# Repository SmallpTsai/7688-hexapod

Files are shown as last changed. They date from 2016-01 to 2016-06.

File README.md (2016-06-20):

# An 18 DOF Hexapod project using LinkIt Smart 7688 + PCA9685

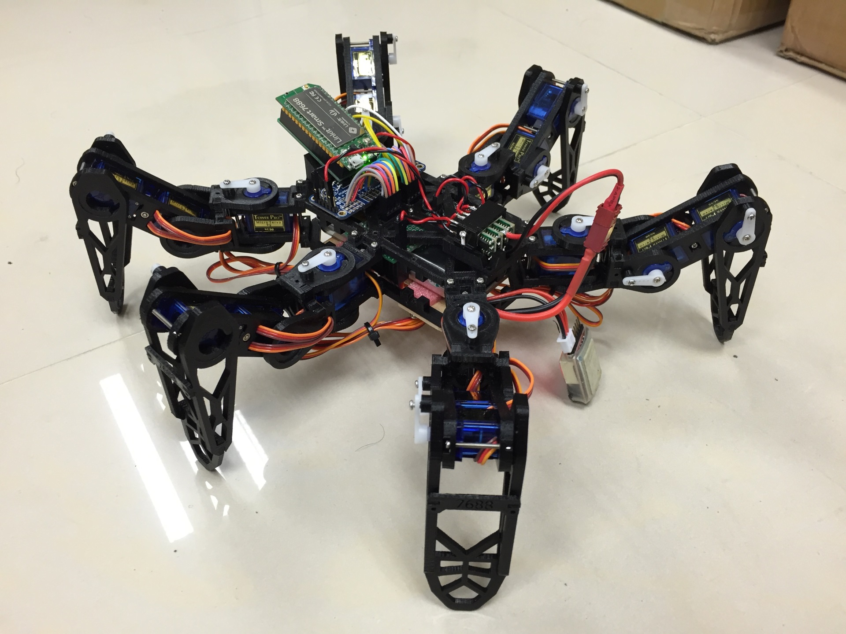
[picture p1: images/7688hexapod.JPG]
7688hexapod


Youtube video1 (http://www.youtube.com/watch?v=CbFrT2eCAvw)
[Youtube video1](https://www.youtube.com/watch?v=CbFrT2eCAvw)

Youtube video2 (http://www.youtube.com/watch?v=70pN0Rd0ca4)
[Youtube video2](https://www.youtube.com/watch?v=70pN0Rd0ca4)

## Hardware

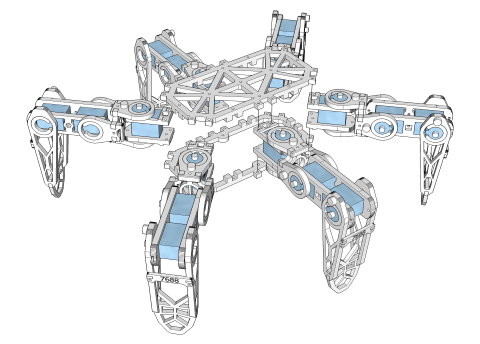
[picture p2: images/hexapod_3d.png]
* Body: 3D printed, go to [STL](STL) folder 
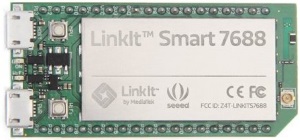
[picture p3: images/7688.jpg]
* [LinkIt Smart 7688](labs.mediatek.com/7688) 
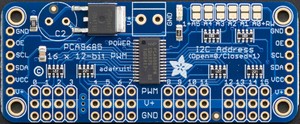
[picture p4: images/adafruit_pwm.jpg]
* [Adafruit 16-channel PWM driver (PCA9685)](https://www.adafruit.com/product/815) 
* SG-90 mini servo x 18 
* DC/DC Buck Voltage regulator (Mini 360 from Taobao/[Amazon](http://www.amazon.com/4-75-23V-1-17V-DC-DC-Converter-Module/dp/B00NJCAI7G)) 
* 2-cell LiPo battery

### Electronics

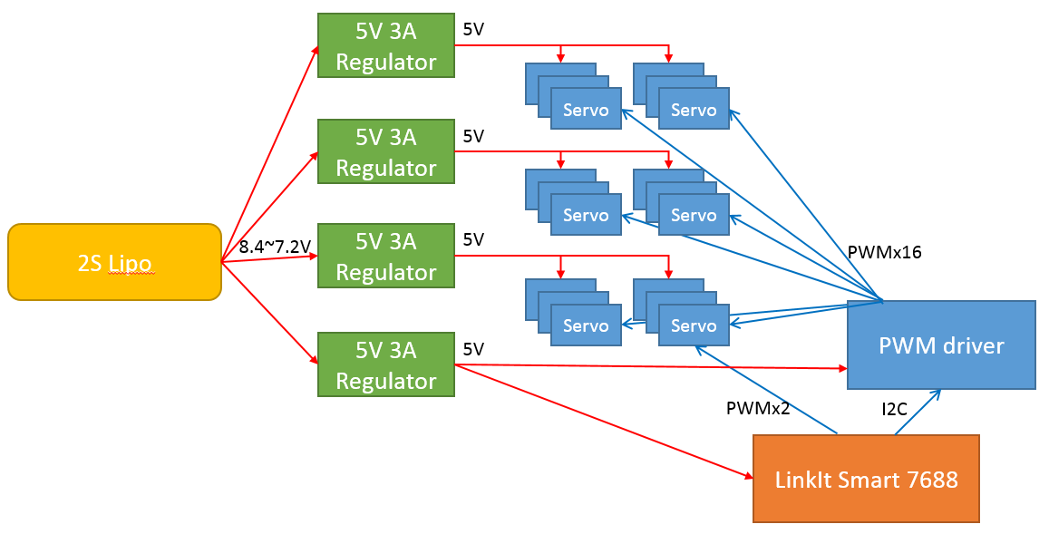
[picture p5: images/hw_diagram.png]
hw_diagram


There are 18 servo controlled by 18 PWM channel, 2 of them are from 7688 itself (GPIO18 & GPIO19), the rest are from the PWM driver connected to 7688 via I2C interface

And 4 DC/DC buck voltage regulator are used because servo draw lots of amount of current (500mA each, 9A total). Each of them provide *3A* current and serve 6 servos (2 legs)
Voltage regulator 1~3 serves all 18 servos
Voltage regulator 4 serves 7688 and PCA9685 (PWM driver IC)

## How to Use/Start

* ssh to 7688 as root
  * as root, do `npm install ws`
  * put `hexapod_core.js`, `hexapod_srv.js` and `settings.js` to `/root`
  * put `index.html` to `/www/hexapod/`
  * edit `/etc/rc.local`, add command `node /root/hexapod_srv.js > /root/log 2>&1 &` before exit 0
* reboot 7688
* open url `http://mylinkit.local/hexapod` on chrome browser
  * make sure client is in the same network with 7688
  * make sure the 7688's device name is mylinkit.local. If not, modify the URL

## Software

### hexapod_core.js

The file contains:
* Logic to control 18 servo via I2C or PWM0/1 (check function `writePwm`)
* IK (inverse kinematics) algorithm (check function `loc2angle`)
* Movement path table (check table `_mode`)
  * There are 9 path now:
    1. `d1`:forward/backward waving ([youtube video](https://youtu.be/CbFrT2eCAvw?t=37))
    2. `d2`:left/right waving ([youtube video](https://youtu.be/CbFrT2eCAvw?t=2))
    3. `d3`:circle waving ([youtube video](https://youtu.be/CbFrT2eCAvw?t=11))
    4. `fwd`:move forward
    5. `bwd`:move backward
    6. `sl`:shift left
    7. `sr`:shift right
    8. `tl`:turn left
    9. `tr`:turn right
  * The path are pre-generated by anohter JS, described later
* The main loop (check function `_next`)

### hexapod_srv.js

The file contains:
* websocket server, receive command from browser (client side)

### index.html

The file contains:
* websocket client, running on browser (client side)

### setting.js

The file contains:
* default settings

### How 7688 control Adafruit PWM driver (PCA9685) via MRAA

First, create an I2C object 
```
var mraa = require("mraa")
var pwms = new mraa.I2c(0)
```

Second, setup I2C address (the default is 0x40, check adafruit's [page](https://learn.adafruit.com/16-channel-pwm-servo-driver/chaining-drivers) for how to set a different address)
```
pwms.address(0x40)
```

Setup PRE_SCALE so that PWM frequency is 61Hz, the period will be 16.37ms, PCA9685 is 12-bit precesion PWM, it has 4096 unit, So it will be `4us` per unit (16.37 / 4096)
According to datasheet, "Writes to PRE_SCALE register are blocked when SLEEP bit is logic 0 (MODE 1)", so a modify/restore MODE0 is required before/after modify PRE_SCALE.
```
pwms.writeReg(0, 0x10)   // SLEEP bit = 1
pwms.writeReg(0xFE, 110) // 61Hz, 16.37ms, ~4us per unit
pwms.writeReg(0, 0x0)    // SLEEP bit = 0
```

According to datasheet, the first 2 registers of each pin are LED_ON, and the other 2 registers are LED_OFF. 
But I found out writing to LED_ON does NOT work. Instead it is inversed, only writing to last 2 register (LED_OFF) works. 
Normal servo operates from 1000us to 2000us: 1500us correspond to center position and 1000/2000us correspond to both end.
The value should be divided by 4 because each unit is 4us. 
```
value = value / 4        // us to unit
pwms.writeReg(6+pin*4, 0);
pwms.writeReg(7+pin*4, 0);
pwms.writeReg(8+pin*4, value & 0xFF);
pwms.writeReg(9+pin*4, (value>>8) & 0xFF);
```

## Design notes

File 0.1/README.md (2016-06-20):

# An 18 DOF Hexapod project using LinkIt Smart 7688 + PCA9685

7688hexapod

[Youtube video1](https://www.youtube.com/watch?v=CbFrT2eCAvw)

[Youtube video2](https://www.youtube.com/watch?v=70pN0Rd0ca4)

## Hardware

* Body: 3D printed, go to [STL](STL) folder 
* [LinkIt Smart 7688](labs.mediatek.com/7688) 
* [Adafruit 16-channel PWM driver (PCA9685)](https://www.adafruit.com/product/815) 
* SG-90 mini servo x 18 
* DC/DC Buck Voltage regulator (Mini 360 from Taobao/[Amazon](http://www.amazon.com/4-75-23V-1-17V-DC-DC-Converter-Module/dp/B00NJCAI7G)) 
* 2-cell LiPo battery

### Electronics

hw_diagram

There are 18 servo controlled by 18 PWM channel, 2 of them are from 7688 itself (GPIO18 & GPIO19), the rest are from the PWM driver connected to 7688 via I2C interface

And 4 DC/DC buck voltage regulator are used because servo draw lots of amount of current (500mA each, 9A total). Each of them provide *3A* current and serve 6 servos (2 legs)
Voltage regulator 1~3 serves all 18 servos
Voltage regulator 4 serves 7688 and PCA9685 (PWM driver IC)

## Software

### hexapod.js

The files contains:
* Logic to control 18 servo via I2C or PWM0/1 (check function `writePwm`)
* IK (inverse kinematics) algorithm (check function `loc2angle`)
* Movement path table (check function `_dance` and array `_danceTable1`)
  * There are 3 path now:
    1. forward/backward waving ([youtube video](https://youtu.be/CbFrT2eCAvw?t=37))
    2. left/right waving ([youtube video](https://youtu.be/CbFrT2eCAvw?t=2))
    3. circle waving ([youtube video](https://youtu.be/CbFrT2eCAvw?t=11))
  * The path are pre-generated by anohter JS, described later
* The main loop (check function `_next`)

### How 7688 control Adafruit PWM driver (PCA9685) via MRAA

First, create an I2C object 
```
var mraa = require("mraa")
var pwms = new mraa.I2c(0)
```

Second, setup I2C address (the default is 0x40, check adafruit's [page](https://learn.adafruit.com/16-channel-pwm-servo-driver/chaining-drivers) for how to set a different address)
```
pwms.address(0x40)
```

Setup PRE_SCALE so that PWM frequency is 61Hz, the period will be 16.37ms, PCA9685 is 12-bit precesion PWM, it has 4096 unit, So it will be `4us` per unit (16.37 / 4096)
According to datasheet, "Writes to PRE_SCALE register are blocked when SLEEP bit is logic 0 (MODE 1)", so a modify/restore MODE0 is required before/after modify PRE_SCALE.
```
pwms.writeReg(0, 0x10)   // SLEEP bit = 1
pwms.writeReg(0xFE, 110) // 61Hz, 16.37ms, ~4us per unit
pwms.writeReg(0, 0x0)    // SLEEP bit = 0
```

According to datasheet, the first 2 registers of each pin are LED_ON, and the other 2 registers are LED_OFF. 
But I found out writing to LED_ON does NOT work. Instead it is inversed, only writing to last 2 register (LED_OFF) works. 
Normal servo operates from 1000us to 2000us: 1500us correspond to center position and 1000/2000us correspond to both end.
The value should be divided by 4 because each unit is 4us. 
```
value = value / 4        // us to unit
pwms.writeReg(6+pin*4, 0);
pwms.writeReg(7+pin*4, 0);
pwms.writeReg(8+pin*4, value & 0xFF);
pwms.writeReg(9+pin*4, (value>>8) & 0xFF);
```

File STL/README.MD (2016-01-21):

## 3D print

Hexapod is assembled by the 3D printeed STL files in this folder. 

#### Leg part:
The required number of each "Leg" is:
* 3d_twist_mount x 1 (x6 = 6)
* 3d_twist_ring x 2 (x6 = 12)
* 3d_twist_ring_b x 2 (x6 = 12)
* 3d_Servo_top x 1 (x6 = 6)
* 3d_Servo_bottom x 1 (x6 = 6)
* 3d_Leg_2xServo_top x 1 (x6 = 6)
* 3d_Leg_2xServo_bottom x 1 (x6 = 6)
* 3d_leg_crew_t x 1 (x6 = 6)
* 3d_leg_crew_b x 1 (x6 = 6)
* 3d_leg_crew_c x 1 (x6 = 6)
* 3d_leg_crew_p x 1 (x6 = 6)

#### Body part:
* 3d_board_up x 1
* 3d_board_bottom x 1

#### Misc part 
(these are optional, depends on how you want to mount electonics part)
* 3d_7688_mount x 1
* 3d_dcdc_mount x 1

## Assemble instruction

#### Leg (exploded view)

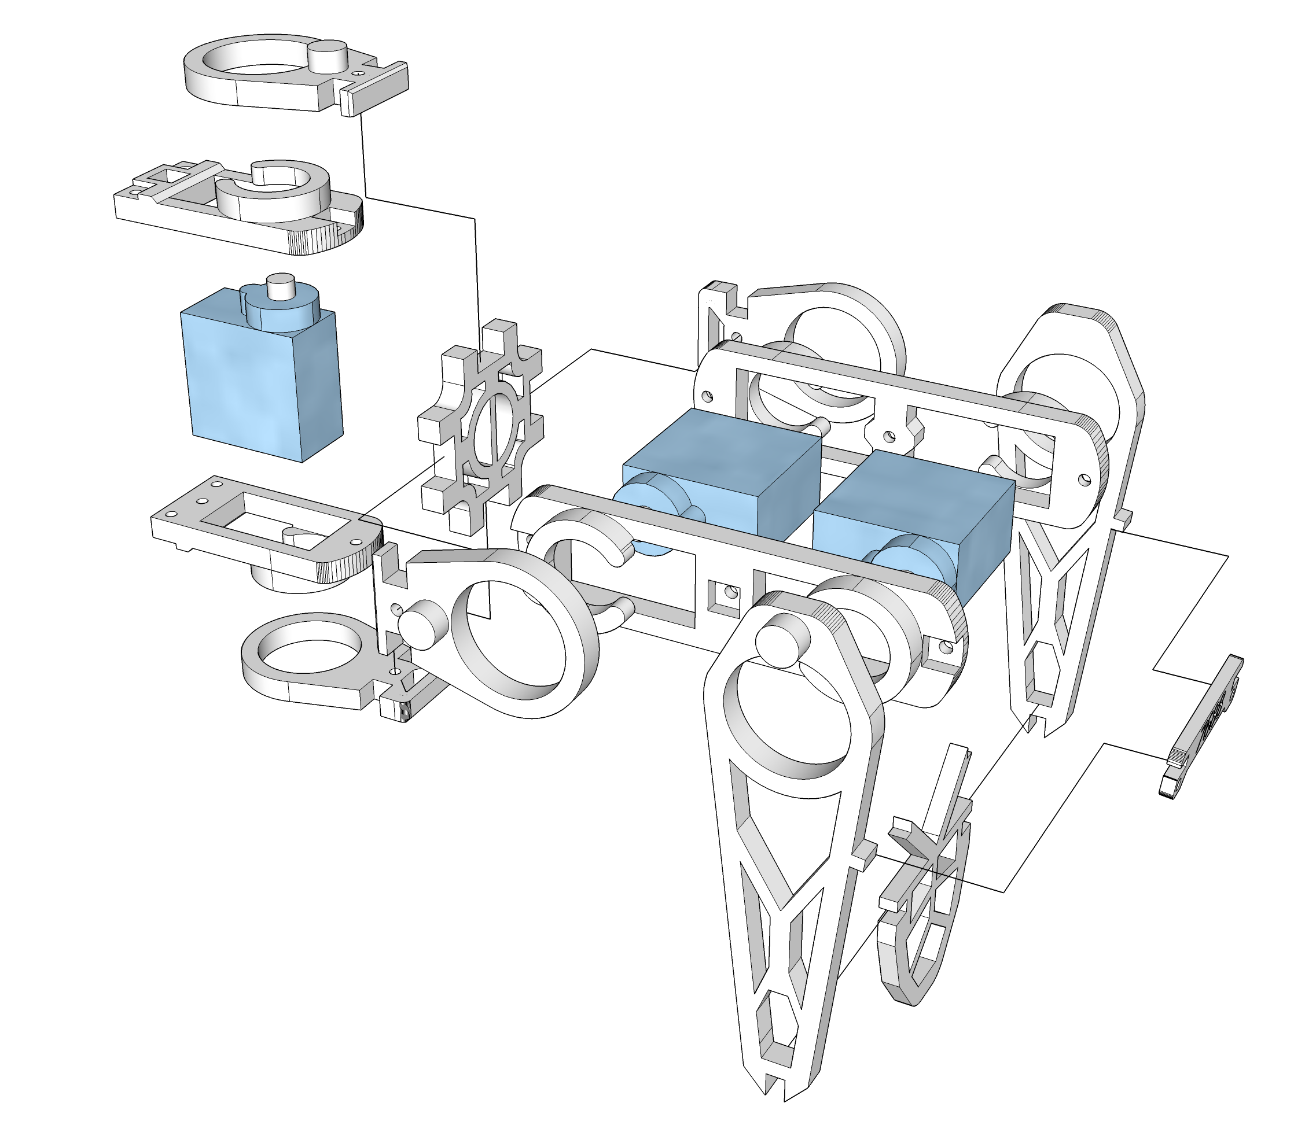
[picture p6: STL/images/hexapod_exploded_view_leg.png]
Leg exploded view


Each leg require:
* M2 screw 20mm x 5 (x6 = 30)
* M2 screw 8mm x 4 (x6 = 24)
* M2 screw 6mm x 3 (x6 = 18)
* M2 nuts x 5 (x6 = 30)

#### Hexapod (exploded view)

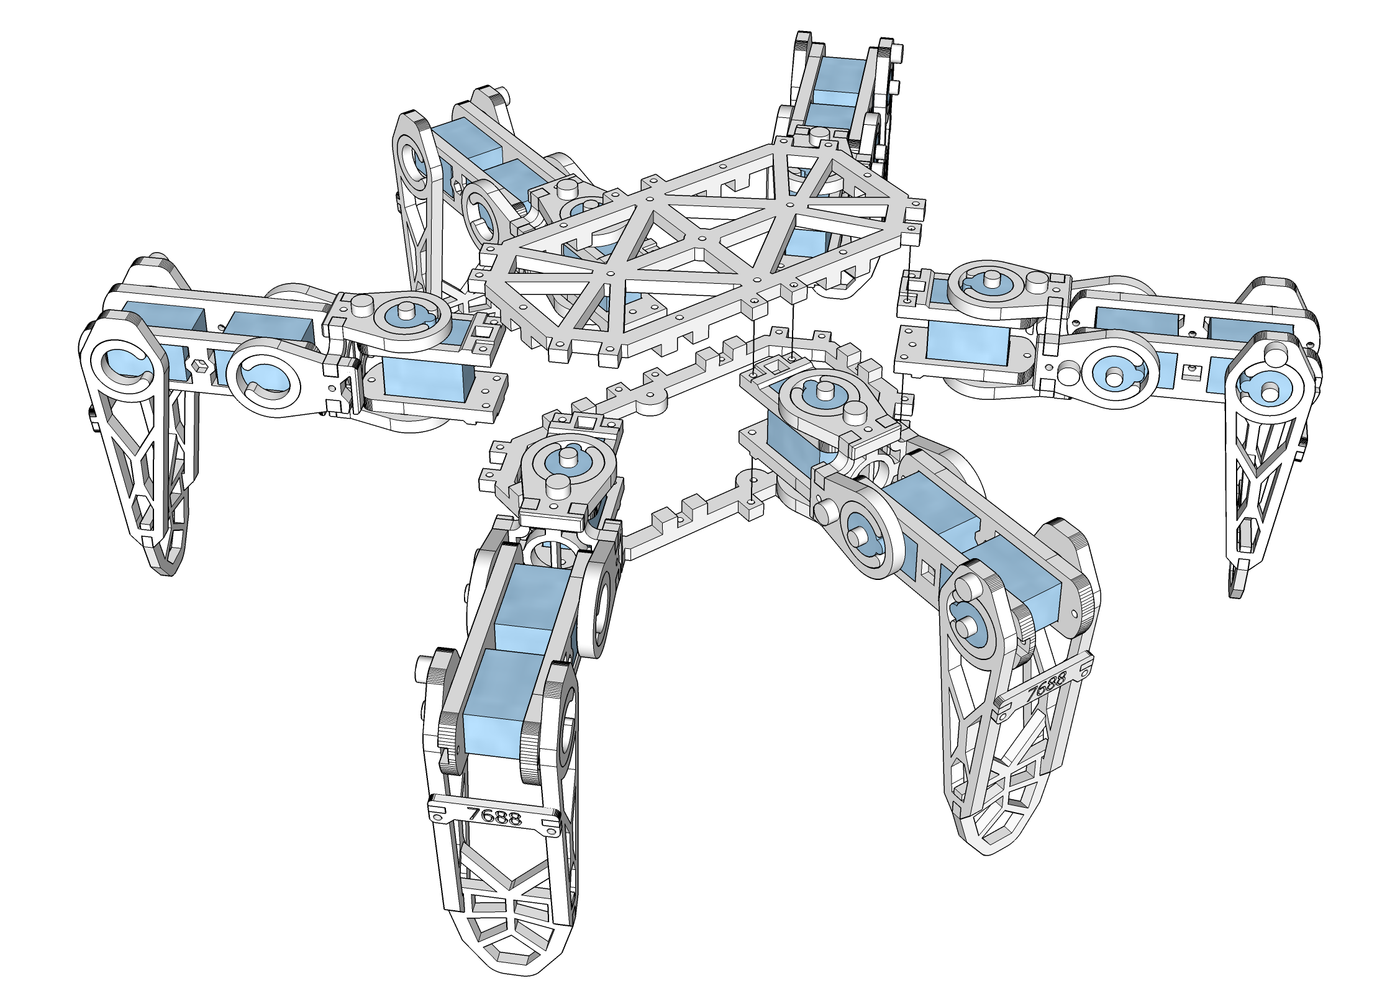
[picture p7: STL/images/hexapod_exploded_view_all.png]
Hexapod exploded view


Still require:
* M2 screw 8mm x 24

to mount all 6 legs onto the body

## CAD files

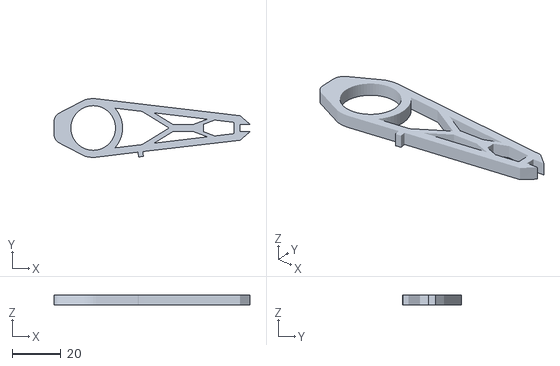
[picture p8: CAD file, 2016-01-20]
STL/3d_leg_crew_b.stl
80.0 x 24.0 x 4.00

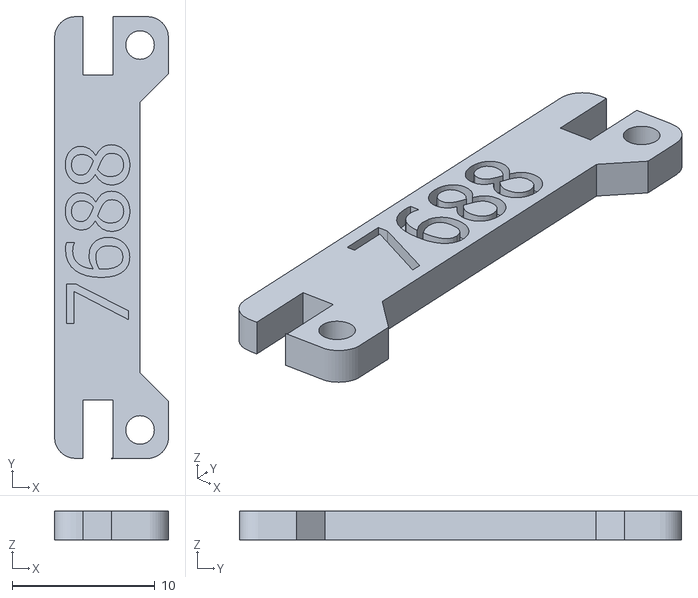
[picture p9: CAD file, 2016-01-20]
STL/3d_leg_crew_p.stl
8.00 x 31.0 x 2.00

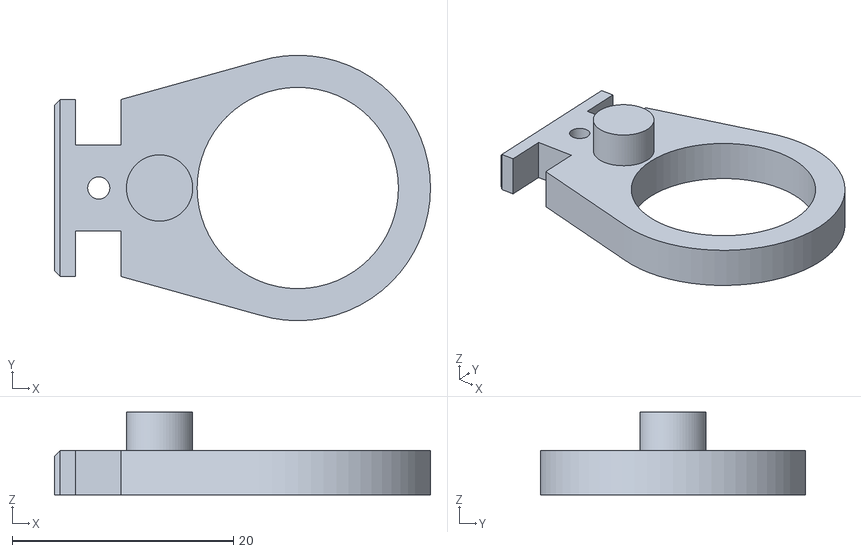
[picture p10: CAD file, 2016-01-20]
STL/3d_twist_ring.stl
34.0 x 24.0 x 7.50

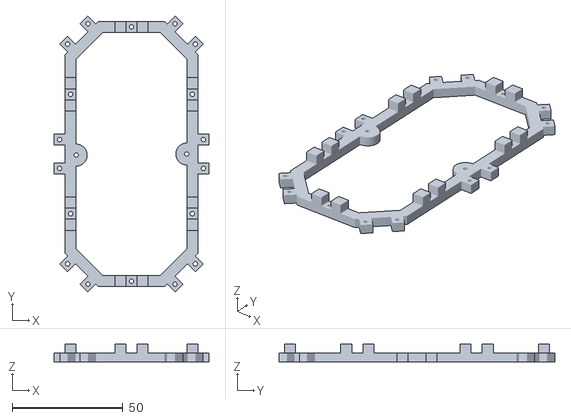
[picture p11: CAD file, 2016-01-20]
STL/3d_board_bottom.stl
70.0 x 124.8 x 8.00

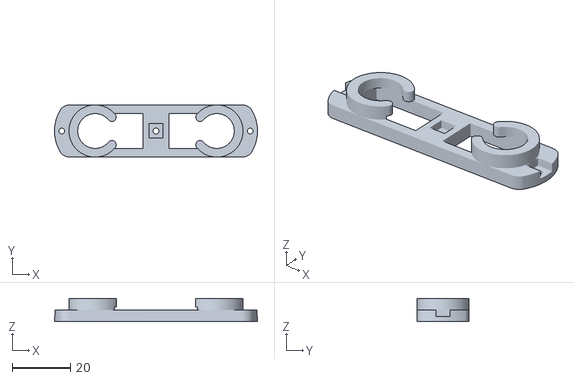
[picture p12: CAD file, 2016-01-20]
STL/3d_Leg_2xServo_top.stl
70.0 x 18.0 x 8.00

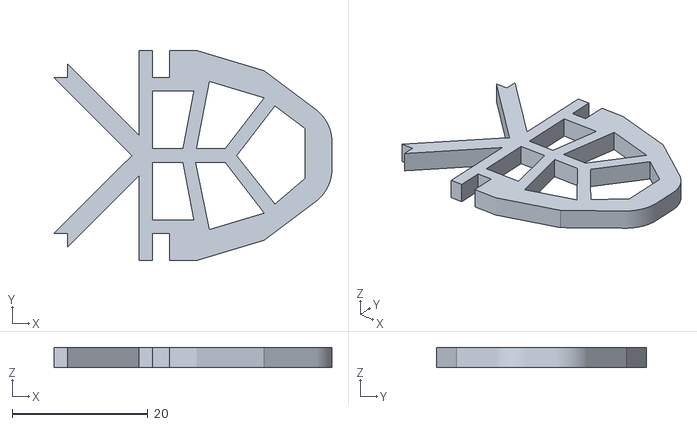
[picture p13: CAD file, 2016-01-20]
STL/3d_leg_crew_c.stl
41.0 x 31.0 x 3.00

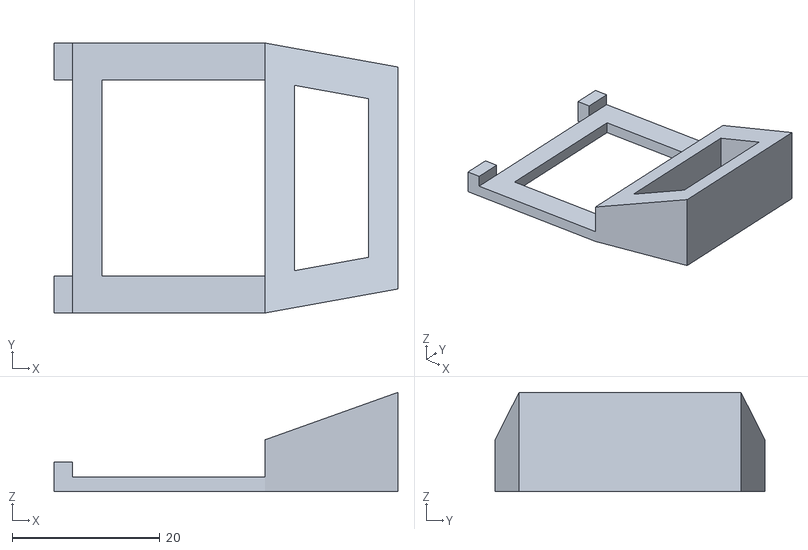
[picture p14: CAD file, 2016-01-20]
STL/3d_7688_mount.stl
46.5 x 36.5 x 13.4

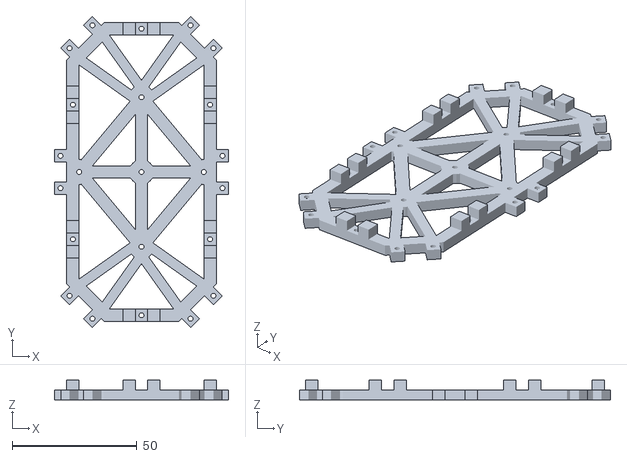
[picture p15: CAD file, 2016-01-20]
STL/3d_board_up.stl
70.0 x 124.8 x 8.00

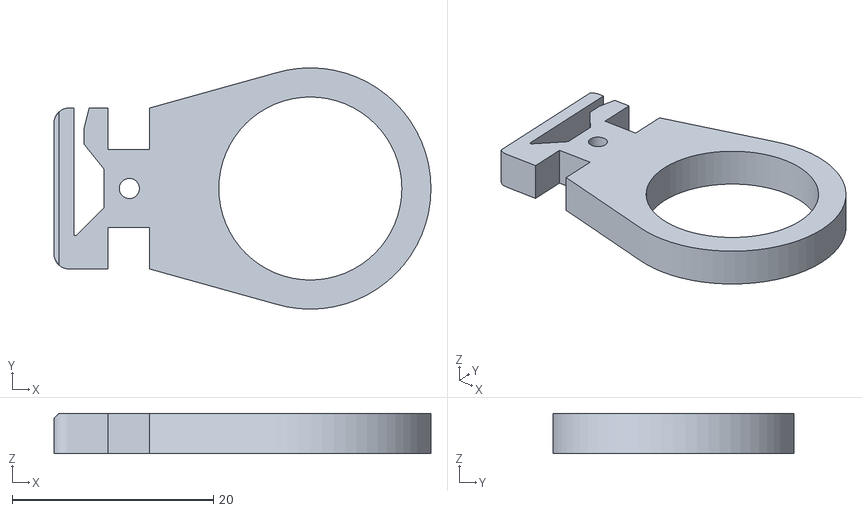
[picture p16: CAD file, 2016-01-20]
STL/3d_twist_ring_b.stl
37.5 x 24.0 x 4.00

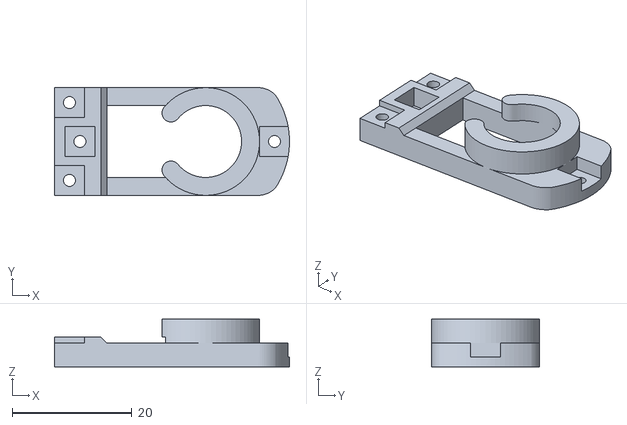
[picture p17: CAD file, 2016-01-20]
STL/3d_Servo_top.stl
39.3 x 18.0 x 8.00

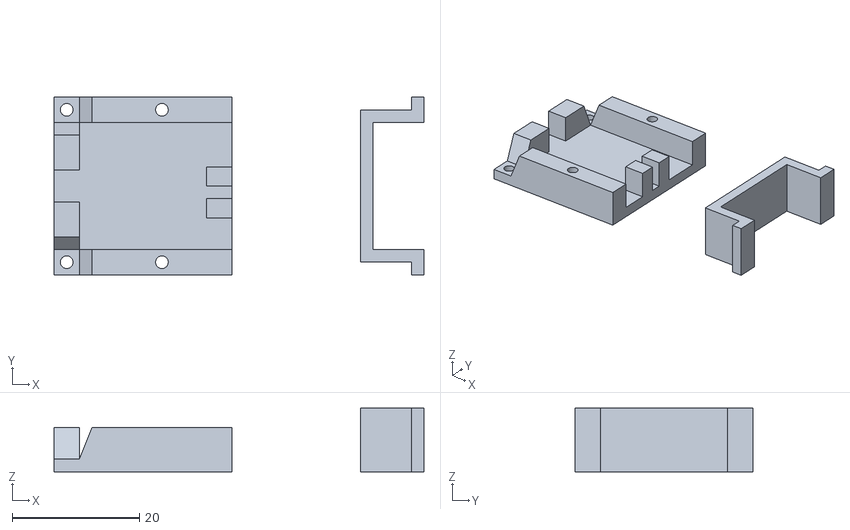
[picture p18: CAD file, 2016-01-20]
STL/3d_dcdc_mount.stl
58.3 x 28.0 x 10.0

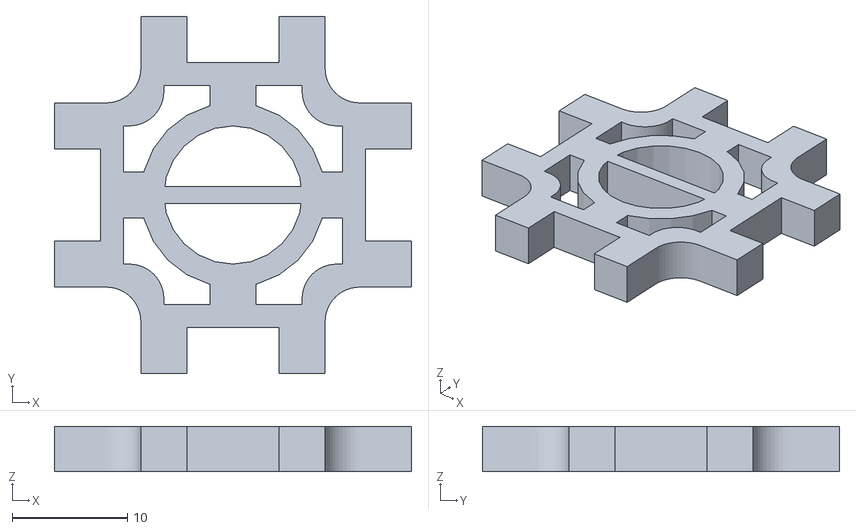
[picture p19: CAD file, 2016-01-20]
STL/3d_twist_mount.stl
31.0 x 31.0 x 3.95

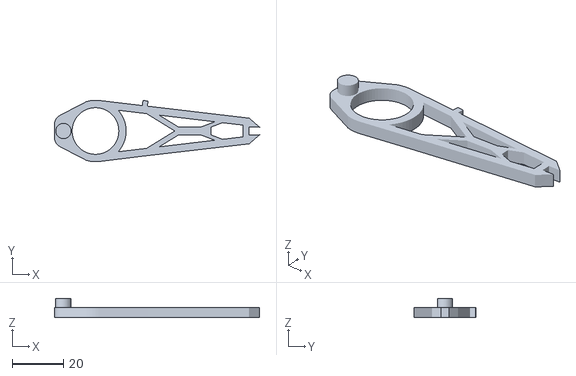
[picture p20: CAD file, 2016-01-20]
STL/3d_leg_crew_t.stl
80.0 x 24.0 x 7.50

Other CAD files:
STL/3d_Servo_bottom.stl
STL/3d_Leg_2xServo_bottom.stl

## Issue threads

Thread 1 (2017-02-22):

Very nice

makefileblog, 2017-02-22:
Great job, I have same project. I'am using arduino, but i would like using too many servos at the same time. With your architecture, can you move servos at the same time ?
Can you use thread on the linkit board ?

Ty

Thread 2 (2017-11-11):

battery specs

alexandre-zia-movile, 2017-11-11:
Hi thanks for sharing this awesome work
Can you please share battery specs?
I don't know which battery to buy.
Thanks

SmallpTsai, 2017-11-12:
hi, I use an 2s lipo battery (7.4v 2500mAh)

alexandre-zia-movile, 2017-11-23:
Thanks!

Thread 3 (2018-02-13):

legs and servos identification

alexandre-zia-movile, 2018-02-13:
Hi,
If you allow me another question.
I have seen in the source code a pin mapping for each leg. But still cant figure out which leg is which.
So I would like to ask you, if you kindly can identify which leg is leg1, leg2, etc.
And also if possible enumerate the servos, which servo is which in the pin mapping.
Thanks again for sharing this awesome project.

alexandre-zia-movile, 2018-02-19:
Figured out my self

Closed 2018-02-19.

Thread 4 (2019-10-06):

7688 hexapod problem: Linkit remains in "Connecting..." mode without ever going into "Connected"

Antonio-C, 2019-10-06:
Ciao SmallpTsai.
Can you direct me to the solution of the following issue?
After following your instructions on how to transfer the files to Linkit Smart 7688, I launch the URL http://mylinkit.local/hexapod  ... The page loads BUT it remains in "**Connecting...**", **I never see "Connected"!**
WiFi net is the same for both Linkit and PC, name is the same on the Linkit and URL...

What can I do to check the situation?
I also see you have a smartphone App to control the Hexapod... where can I find it?
Thanks,
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

A

Gwendam-753, 2020-04-22:
Hello, Antonio,
I don't send you this comment to help you but I need some advice (I'm doing the hexapod)...
Did you do this project ?
Can you show me the electronic circuits you made for the hexapod (power supply etc... You can send me a picture if you want) ?
Thanks a lot for your answer :)

Antonio-C, 2020-11-15:
Ciao Gwendam,
sorry, but I had to suspend my project. I still face the "connecting problem"... If/when I will be able to solve that problem, I will be very happy to share my progress with you.
Kind regards,

Antonio

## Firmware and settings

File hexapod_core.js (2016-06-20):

var _modeTable = {
  modeAdjust: "adj",
  modeStop: "s",
  modeDance1: "d1",
  modeDance2: "d2",
  modeDance3: "d3",
  modeDemo: "demo",
  modeFwd: "fwd",
  modeBwd: "bwd",
  modeTurnLeft: "tl",
  modeTurnRight: "tr",
  modeShiftLeft: "sl",
  modeShiftRight: "sr",
}

var DEBUG = false
var DEBUG_EMU = false

var settings = require("./settings.js")

// ==========================================================================
// low level HW control

if(!DEBUG_EMU) {
  var mraa = require("mraa")
  var pwms = new mraa.I2c(0)
  var pwm0 = new mraa.Pwm(18)
  var pwm1 = new mraa.Pwm(19)
  var pGood = new mraa.Gpio(0)
  var pError = new mraa.Gpio(1)

  pwms.address(0x40)
  pwms.writeReg(0, 0x10)
  pwms.writeReg(0xFE, 83) // 81Hz, ~12.3ms, ~3us per unit
  pwms.writeReg(0, 0x0)

  pwm0.period_ms(10)
  pwm0.enable(true)
  pwm1.period_ms(10)
  pwm1.enable(true)

  pGood.dir(0)
  pGood.write(0)
  pError.dir(0)
  pError.write(0)
}

// pin = 0~17
// value = us
function writePwm(pin, value)
{
  if(DEBUG_EMU)
    return
  if(pin < 16)
  {
    var r
    value = parseInt(value / 3);
    r = pwms.writeReg(6+pin*4, 0);
    if(r != 0)
    {
      pGood.write(0)
      pError.write(1)
      throw "<** PANIC **> failed to write PWM to I2C device!!!"
    }
    pwms.writeReg(7+pin*4, 0);
    pwms.writeReg(8+pin*4, value & 0xFF);
    pwms.writeReg(9+pin*4, (value>>8) & 0xFF);
  }
  else if(pin == 16)
  {
    pwm0.pulsewidth_us(value)
  }
  else if(pin == 17)
  {
    pwm1.pulsewidth_us(value)
  }
}

// ==========================================================================
// middleware
//
//  coordinates:
//    x: >0=left, <0=right 
//    y: >0=front, <0=back
//    z: >0=height
//    origin = body center


// x, y, z coordinates of nodes of each leg 
var legCenters = [
  [40.36, 70.36, 0],
  [55.25, 0, 0],
  [40.36, -70.36, 0],
  [-40.36, -70.36, 0],
  [-55.25, 0, 0],
  [-40.36, 70.36, 0],
];

var legAngles = [45, 0, 315, 225, 180, 135]

// default x, y, z coordinates of tips of each leg 
var legTipsDefault = [
  [95.52, 125.52, -62, 1],
  [133.25, 0, -62, 1],
  [95.52, -125.52, -62, 1],
  [-95.52, -125.52, -62, 1],
  [-133.25, 0, -62, 1],
  [-95.52, 125.52, -62, 1],
];

// "current" x, y, z coordinates of tips of each leg 
var legTipsLoc = [
  [0, 0, 0],
  [0, 0, 0],
  [0, 0, 0],
  [0, 0, 0],
  [0, 0, 0],
  [0, 0, 0],
];

// return angles 0, 1, 2 of specified "leg" for its tip to reach specified "location"
// return null if impossible
function loc2angles(leg, loc)
{
  const a = 42, b = 84, c = 36

  // shift origin to leg center
  x = loc[0] - legCenters[leg][0]
  y = loc[1] - legCenters[leg][1]
  z = loc[2] - legCenters[leg][2]

  a0 = (180/Math.PI)*Math.atan(y/x) - legAngles[leg]
  if(x<0)
    a0 += 180
  else if(y<0)
    a0 += 360
  if(a0 > 180)
    a0 -= 360

  xp = Math.sqrt(x*x+y*y)-c
  yp = z

  lr = Math.sqrt(xp*xp+yp*yp)
  ar = (180/Math.PI)*Math.asin(yp/lr)
  at = (180/Math.PI)*Math.acos((lr*lr + a*a - b*b)/(2*a*lr))
  az = (180/Math.PI)*Math.acos((lr*lr - a*a + b*b)/(2*b*lr))
  a1 = at + ar
  a2 = 180 - at - az

  if(0) {
    console.log("\nxyz = " + x + "," + y + "," + z)
    console.log("len of reach = " + lr)
    console.log("angle of reach = " + ar)
    console.log("angle1 = " + at)
    console.log("angle2 = " + az)
    console.log("result = " + a0 + "," + a1 + "," + a2)
  }

  return [a0, a1, a2]
}

// nonblockingly move tip of specified "leg" to specified "location"
// return true if ok
// return false if impossible
function moveLeg(leg, loc)
{
  a = loc2angles(leg, loc)

  if(a[0] <= 45 && a[0] >= -45 &&
      a[1] <= 90 && a[1] >= -90 &&
      a[2] <= 150 && a[2] >= 36)
  {
    writePwm(settings.pinMap[leg][0], settings.pinDefaultPWM[leg][0] + a[0] * 500 / 45)
    writePwm(settings.pinMap[leg][1], settings.pinDefaultPWM[leg][1] - a[1] * 500 / 45)
    writePwm(settings.pinMap[leg][2], settings.pinDefaultPWM[leg][2] + (a[2]-90) * 500 / 45)  
    legTipsLoc[leg][0] = loc[0]
    legTipsLoc[leg][1] = loc[1]
    legTipsLoc[leg][2] = loc[2]
  }
  else
  {
    console.log("moveLeg failed: " + leg + "," + loc + "," + a)
    return false
  }

  return true;
}

// return current tip location (in x, y, z) of specified "location"
function getLegsLoc(leg)
{
  return legTipsLoc[leg].slice(0, 3)
}

// ==========================================================================
// high level control
//

function _adjust(leg, time, params, loc) {

  loc[0] = 0
  loc[1] = 0
  loc[2] = -20

  return time
}

function _stop(leg, time, params, loc) {

  loc[0] = 0
  loc[1] = 0
  loc[2] = 0

  return time
}
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

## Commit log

2016-01-20 3d files commit
    [3d_7688_mount.stl, 3d_Leg_2xServo_bottom.stl, 3d_Leg_2xServo_top.stl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]
2016-01-21 renamed: STL/images/hexapod_explode_view_all.png -> STL/images/hexapod_exploded_view_all.png
